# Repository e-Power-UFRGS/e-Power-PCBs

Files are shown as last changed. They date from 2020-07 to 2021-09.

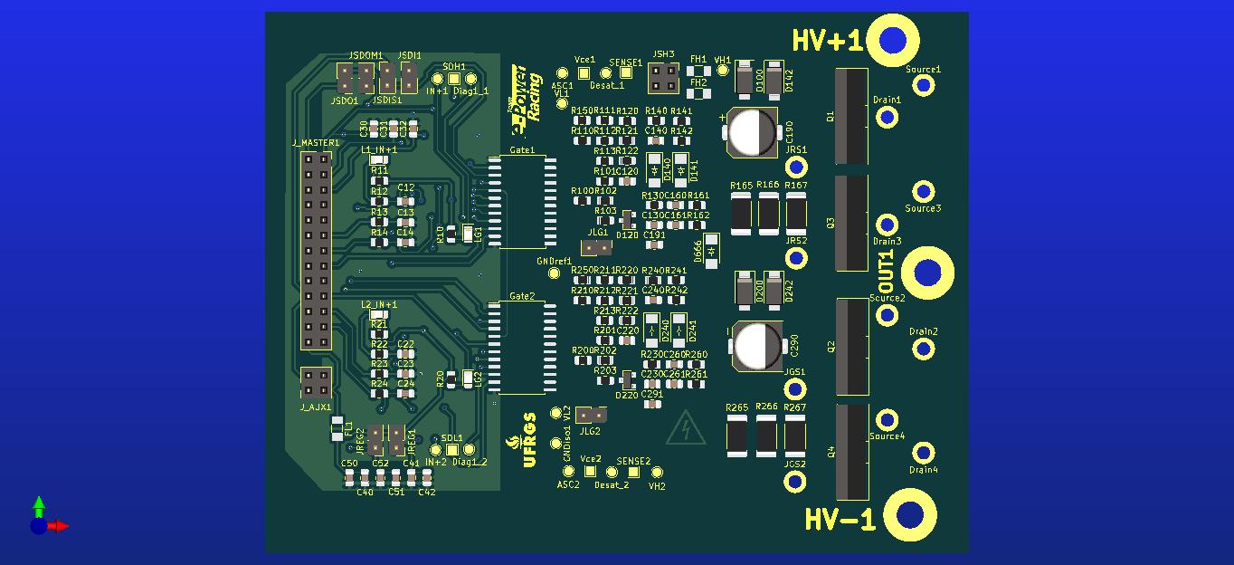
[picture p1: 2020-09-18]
Inversor/Gate_Driver_V2.jpg

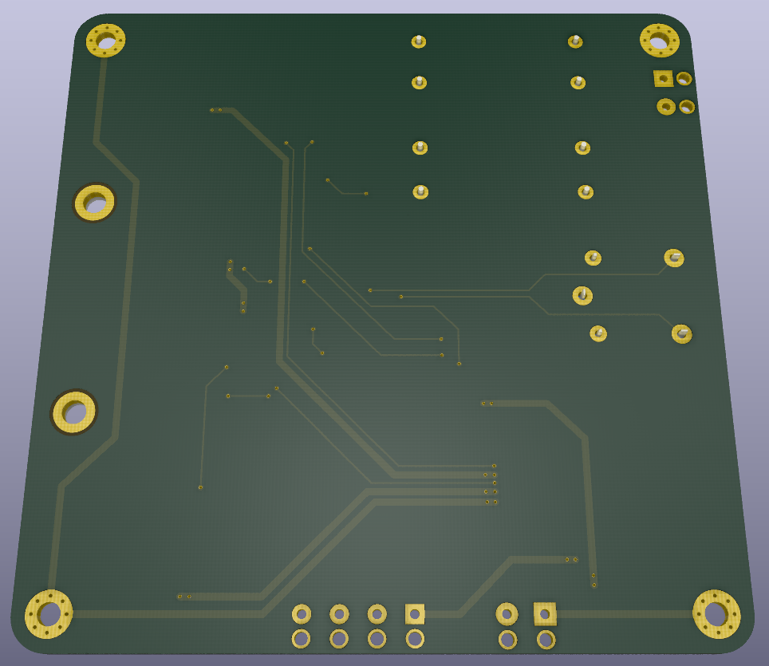
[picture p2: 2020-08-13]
TSAL/3d-renders/Screenshot_297.png

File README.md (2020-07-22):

# e-Power-PCBs

## Index

#### e-Power_conventions: Standard conventions for all PCBs
The image shows an example with conventions regarding the description data of the PCBs. One way to implemment this conventions is oppening 2 KiCad Pcbnew windows, one with the file you want to update and other with the e-Power_conventions.kicad_pcb and the copy the standard from one window to the other (yes, this is possible on the current versions of KiCad!).

descriptive_conventions

#### BMS_20S: Battery Management System with 20S measurement capability

#### TSAL: Tractive System Alternating Lights 

## License
[MIT](https://choosealicense.com/licenses/mit/)

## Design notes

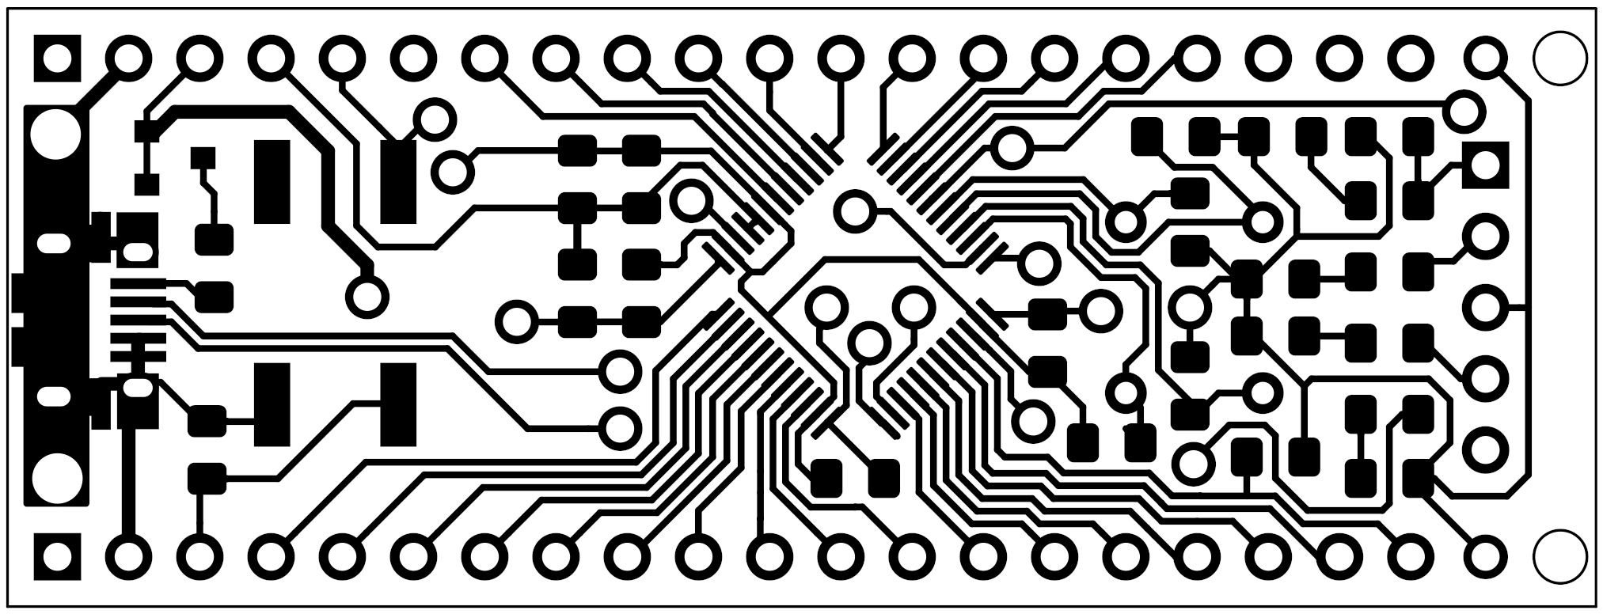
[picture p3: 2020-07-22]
UFRGS-PILL/front/UFRGS PILL-brd.jpg

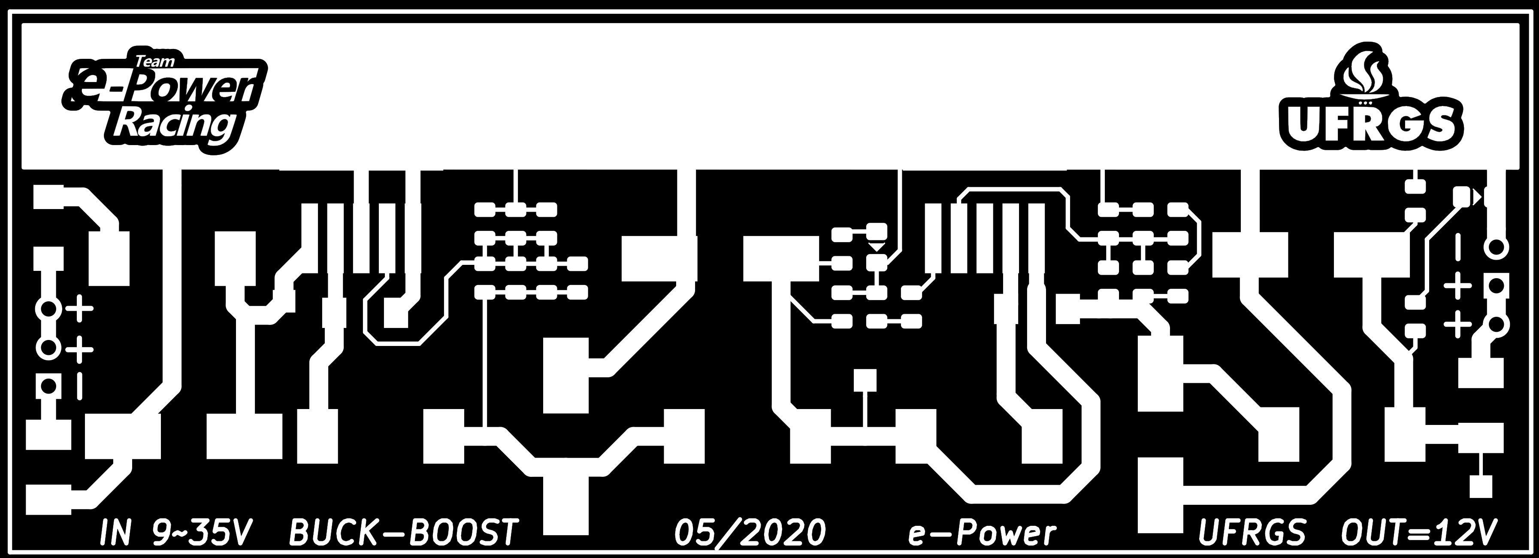
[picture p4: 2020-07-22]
BUCK-BOOST/BUCK-BOOST KiCad-brd_invert.jpg

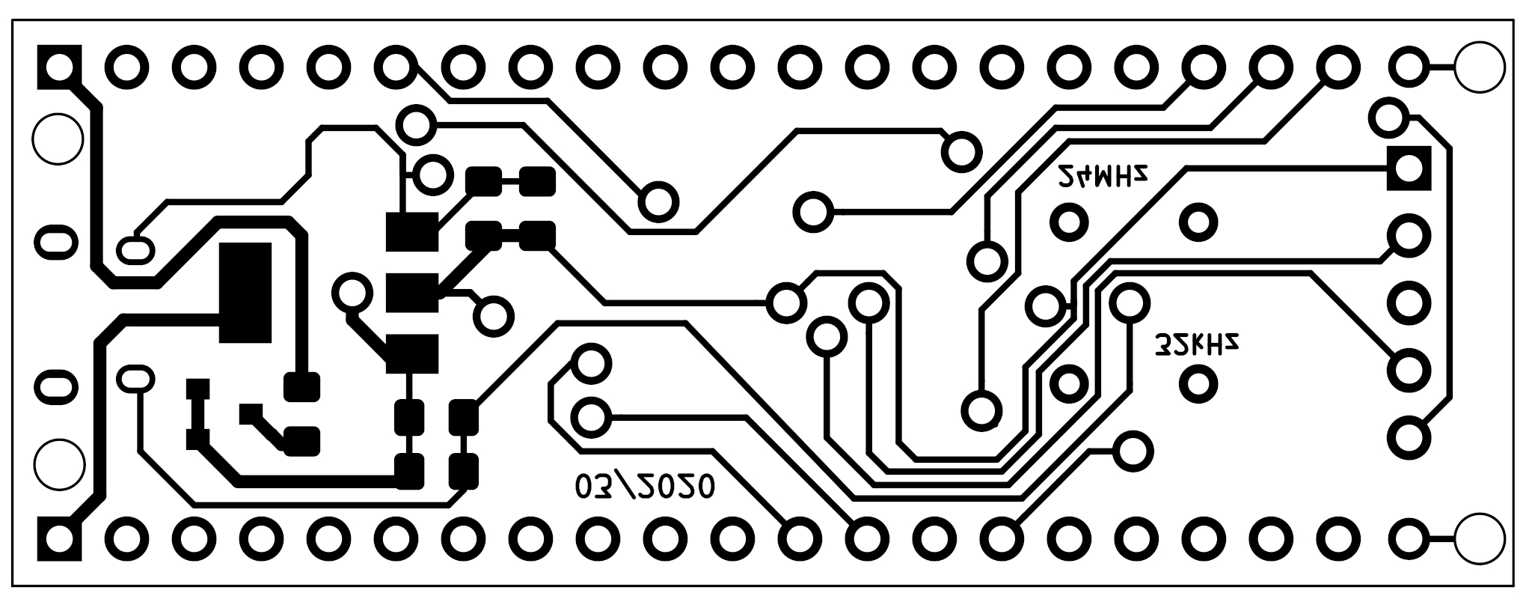
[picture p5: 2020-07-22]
UFRGS-PILL/back/UFRGS PILL-brd.jpg

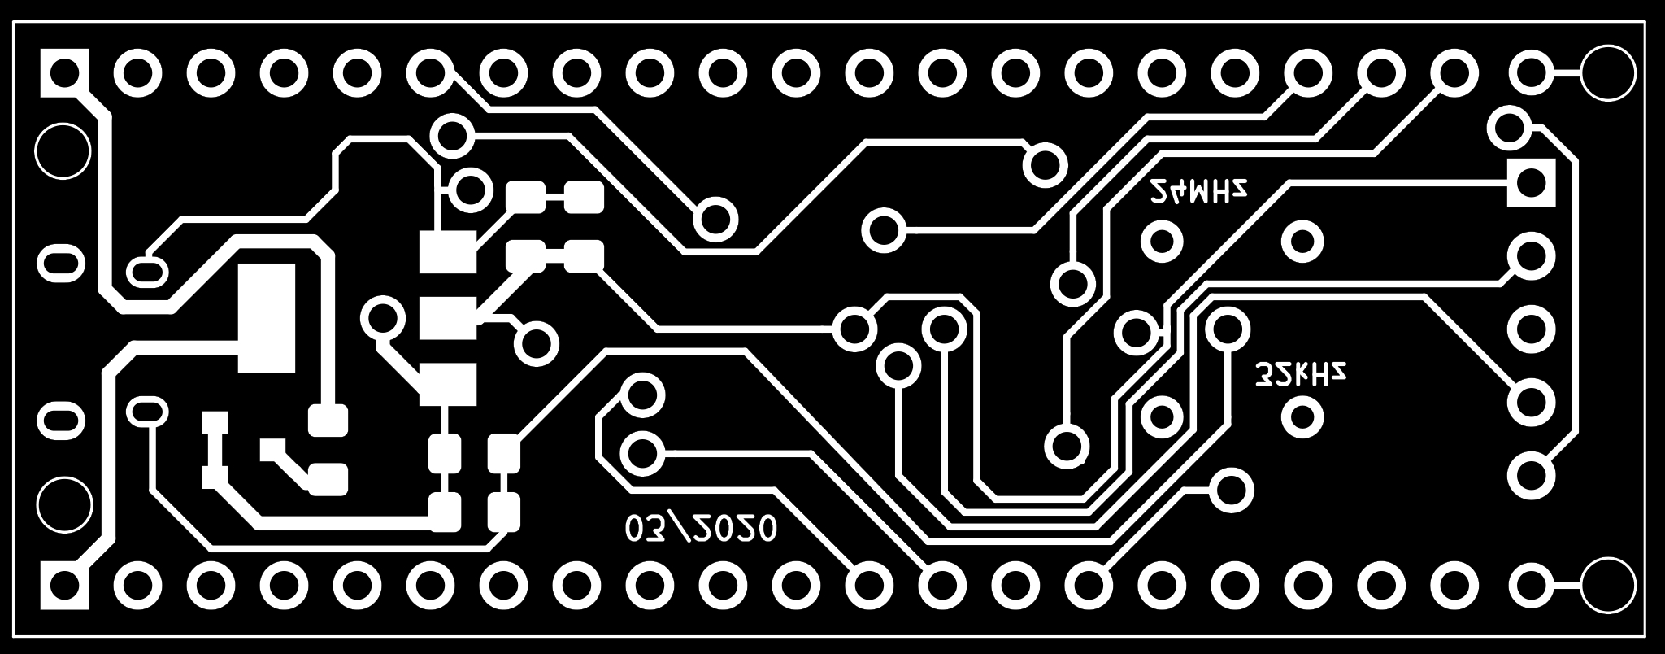
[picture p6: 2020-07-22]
UFRGS-PILL/back/UFRGS PILL-brd_invert.jpg

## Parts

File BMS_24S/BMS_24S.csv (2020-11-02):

Reference | Quantity | Value | Footprint | Datasheet | LCSC | Power | Precision | Voltage
C106 C103 C101 C107 C104 C102 C108 C113 C118 C126 C125 C115 C119 C120 C121 C122 C105 C116 C117 C206 C201 C207 C204 C209 C211 C301 C306 C309 C501 C502 C503 C601 C602 C603 C701 C702 C703 C801 C802 C803 C901 C902 C903 C1001 C1002 C1003 C1101 C1102 C1103 C1201 C1202 C1203 C1301 C1302 C1303 C1401 C1402 C1403 C1501 C1502 C1503 C1601 C1602 C1603 C1801 C1901 C2001 C2101 C2201 C2301 C3101 | 71 | 100nF | Capacitor_SMD:C_0805_2012Metric | https://datasheet.lcsc.com/szlcsc/YAGEO-CC0805KRX7R9BB104_C49678.pdf | C49678 |  | 10% | 50V
C109 C110 | 2 | 12pF | Capacitor_SMD:C_0805_2012Metric | Guangdong-Fenghua-Advanced-Tech-0805CG120J500NT_C1792.pdf | C1792 |  | 10% | 50V
C112 C111 | 2 | 100pF | Capacitor_SMD:C_0805_2012Metric | Samsung-Electro-Mechanics-CL21C101JBANNNC_C1790.pdf | C1790 |  | 10% | 50V
C114 C123 C124 C127 C205 C208 C202 C203 C210 C302 | 10 | 10uF | Capacitor_SMD:C_0805_2012Metric | ~ | C15850
C303 C307 C304 C305 C308 | 5 | 220uF | Capacitor_SMD:CP_Elec_10x10 | ~
D108 D107 D106 D105 D104 D103 D102 D101 D302 D2503 D2504 D2502 D2501 D2603 D2604 D2602 D2601 D2703 D2704 D2702 D2701 D2803 D2804 D2802 D2801 D2903 D2904 D2902 D2901 D3003 D3004 D3002 D3001 | 33 | LED | e-Power:LED_0805_1.15x1.40mm_HandSolder | ~
D301 | 1 | SS54HF | e-Power:DO-214AC | https://www.diodes.com/assets/Datasheets/ds23001.pdf
D501 D502 D503 D504 D505 D506 D601 D602 D603 D604 D605 D606 D701 D702 D703 D704 D705 D706 D801 D802 D803 D804 D805 D806 D901 D902 D903 D904 D905 D906 D1001 D1002 D1003 D1004 D1005 D1006 D1101 D1102 D1103 D1104 D1105 D1106 D1201 D1202 D1203 D1204 D1205 D1206 D1301 D1302 D1303 D1304 D1305 D1306 D1401 D1402 D1403 D1404 D1405 D1406 D1501 D1502 D1503 D1504 D1505 D1506 D1601 D1602 D1603 D1604 D1605 D1606 | 72 | LL4148 | e-Power:SOD-80 | http://www.vishay.com/docs/85557/ll4148.pdf | C9808
F301 | 1 | Fuse_1206 | e-Power:FUSE_1206_3216Metric | ~
F414 F416 F420 F422 F424 F426 F425 F423 F421 F419 F417 F415 F413 F411 F409 F407 F405 F403 F401 F402 F404 F406 F408 F410 F412 F418 | 26 | Fuse | e-Power:FUSE_1206_3216Metric | ~
FB101 FB301 FB302 FB303 FB304 FB305 FB306 FB307 FB308 FB309 FB310 | 11 | Ferrite_Bead | e-Power:FB_0805_2012Metric | ~ | C1017
G101 | 1 | Logo_UFRGS_Large | e-Power:Logo_UFRGS_22.0x12.0mm_Mask
G102 | 1 | Logo_e-Power_Large | e-Power:Logo_e-Power_22.8x12.0mm_SilkS
G103 | 1 | Logo_UFRGS_Large | e-Power:Logo_UFRGS_22.0x12.0mm_SilkS
G104 | 1 | SYM_LASER_Large | Symbol:WEEE-Logo_8.4x12mm_SilkScreen | ~
G105 | 1 | SYM_LASER_Large | Symbol:KiCad-Logo_12mm_SilkScreen | ~
G106 | 1 | SYM_ESD_Large | Symbol:ESD-Logo_13.2x12mm_SilkScreen | ~
H101 H102 H103 H104 | 4 | GND | e-Power:MountingHole_3.2mm_M3_Pad_Via | ~
J101 | 1 | Conn_01x08_Male | e-Power:Molex_Mini-Fit_Jr_2x04_P4.20mm_Horizontal | ~
J102 | 1 | ST-LINK | Connector_PinHeader_2.54mm:PinHeader_1x05_P2.54mm_Vertical | ~
J1701 | 1 | TEMP_IDC_26_CONN | Connector_IDC:IDC-Header_2x13_P2.54mm_Horizontal | ~
J3101 | 1 | Current_Conn | Connector_PinHeader_2.54mm:PinHeader_1x04_P2.54mm_Horizontal | ~
J3102 | 1 | BSPD_Conn | Connector_PinHeader_2.54mm:PinHeader_1x04_P2.54mm_Horizontal | ~
J401 | 1 | VOLT_IDC_26_CONN | Connector_IDC:IDC-Header_2x13_P2.54mm_Horizontal | ~
JP3101 | 1 | Jumper | Jumper:SolderJumper-2_P1.3mm_Open_TrianglePad1.0x1.5mm | ~
JP501 JP503 JP502 JP601 JP603 JP602 JP701 JP703 JP702 JP801 JP803 JP802 JP901 JP903 JP902 JP1001 JP1003 JP1002 JP1101 JP1103 JP1102 JP1201 JP1203 JP1202 JP1301 JP1303 JP1302 JP1401 JP1403 JP1402 JP1501 JP1503 JP1502 JP1601 JP1603 JP1602 | 36 | 0R | e-Power:zero_ohm_resistor_0805 | ~ |  | 1/8W | 1% | 150V
Q101 | 1 | MMBT3904 | Package_TO_SOT_SMD:SOT-23 | Changjiang-Electronics-Tech-CJ-MMBT5401_C8326.pdf | C20526
Q201 | 1 | MMBT5401 | Package_TO_SOT_SMD:SOT-23 | https://datasheet.lcsc.com/szlcsc/Changjiang-Electronics-Tech-CJ-MMBT5401_C8326.pdf | C8326
Q2501 Q2502 Q2503 Q2504 Q2601 Q2602 Q2603 Q2604 Q2701 Q2702 Q2703 Q2704 Q2801 Q2802 Q2803 Q2804 Q2901 Q2902 Q2903 Q2904 Q3001 Q3002 Q3003 Q3004 | 24 | Si2302DS | Package_TO_SOT_SMD:SOT-23 | https://www.vishay.com/docs/70628/70628.pdf
R107 R105 R101 R108 R106 R102 R149 R147 R139 R137 R121 R119 R133 R132 R131 R130 R103 R129 R128 R127 R126 R216 R217 R218 R229 R212 R219 R204 R214 R221 R206 R226 R228 R225 R208 R202 R215 R313 R301 R302 R303 R305 R306 R506 R504 R503 R502 R501 R508 R507 R514 R512 R511 R510 R509 R513 R516 R515 R505 R606 R604 R603 R602 R601 R608 R607 R614 R612 R611 R610 R609 R613 R616 R615 R605 R706 R704 R703 R702 R701 R708 R707 R714 R712 R711 R710 R709 R713 R716 R715 R705 R806 R804 R803 R802 R801 R808 R807 R814 R812 R811 R810 R809 R813 R816 R815 R805 R906 R904 R903 R902 R901 R908 R907 R914 R912 R911 R910 R909 R913 R916 R915 R905 R1006 R1004 R1003 R1002 R1001 R1008 R1007 R1014 R1012 R1011 R1010 R1009 R1013 R1016 R1015 R1005 R1106 R1104 R1103 R1102 R1101 R1108 R1107 R1114 R1112 R1111 R1110 R1109 R1113 R1116 R1115 R1105 R1206 R1204 R1203 R1202 R1201 R1208 R1207 R1214 R1212 R1211 R1210 R1209 R1213 R1216 R1215 R1205 R1306 R1304 R1303 R1302 R1301 R1308 R1307 R1314 R1312 R1311 R1310 R1309 R1313 R1316 R1315 R1305 R1406 R1404 R1403 R1402 R1401 R1408 R1407 R1414 R1412 R1411 R1410 R1409 R1413 R1416 R1415 R1405 R1506 R1504 R1503 R1502 R1501 R1508 R1507 R1514 R1512 R1511 R1510 R1509 R1513 R1516 R1515 R1505 R1606 R1604 R1603 R1602 R1601 R1608 R1607 R1614 R1612 R1611 R1610 R1609 R1613 R1616 R1615 R1605 R1803 R1801 R1804 R1802 R1903 R1901 R1904 R1902 R2003 R2001 R2004 R2002 R2103 R2101 R2104 R2102 R2203 R2201 R2204 R2202 R2303 R2301 R2304 R2302 R2543 R2529 R2515 R2501 R2643 R2629 R2615 R2601 R2743 R2729 R2715 R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 | 283 | 1K | Resistor_SMD:R_0805_2012Metric | https://datasheet.lcsc.com/szlcsc/Uniroyal-Elec-0805W8F1001T5E_C17513.pdf | C17513 | 1/8W | 1% | 150V
R110 R201 R210 | 3 | 100R | Resistor_SMD:R_0805_2012Metric | Uniroyal-Elec-0805W8F1000T5E_C17408.pdf | C17408 | 1/8W | 1% | 150V
R112 R111 | 2 | 10R | Resistor_SMD:R_0805_2012Metric | 1812121441_Uniroyal-Elec-0805W8F100JT5E_C17415.pdf | C17415 | 1/8W | 1% | 150V
R114 R115 R116 R117 R113 R118 R124 R125 R134 R135 R123 R136 R142 R143 R144 R145 R141 R146 R150 R148 R140 R138 R122 R120 R109 R104 R230 R224 R2556 R2542 R2528 R2514 R2656 R2642 R2628 R2614 R2756 R2742 R2728 R2714 R2856 R2842 R2828 R2814 R2956 R2942 R2928 R2914 R3056 R3042 R3028 R3014 R3103 R3104 R3105 R3102 | 56 | 10K | Resistor_SMD:R_0805_2012Metric | https://datasheet.lcsc.com/szlcsc/Uniroyal-Elec-0805W8F1001T5E_C17513.pdf | C17414 | 1/8W | 1% | 150V
R209 R220 R203 R222 R223 R227 R213 R1702 R1703 R1704 R1705 R1706 R1707 R1708 R1709 R1710 R1711 R1712 R1715 R1713 R1714 R1716 R1717 R1718 R1719 R1720 R1721 R1722 R1723 R1724 R1725 R1726 R1701 R3101 | 34 | 0R | Resistor_SMD:R_0805_2012Metric | ~ | C17477
R211 R205 R207 | 3 | 100K | Resistor_SMD:R_0805_2012Metric | ~ | C17407
R2549 R2550 R2551 R2552 R2553 R2548 R2547 R2535 R2536 R2537 R2538 R2539 R2534 R2533 R2521 R2522 R2523 R2524 R2525 R2520 R2519 R2507 R2508 R2509 R2506 R2505 R2510 R2511 R2504 R2503 R2502 R2518 R2517 R2516 R2532 R2531 R2530 R2546 R2545 R2544 R2649 R2650 R2651 R2652 R2653 R2648 R2647 R2635 R2636 R2637 R2638 R2639 R2634 R2633 R2621 R2622 R2623 R2624 R2625 R2620 R2619 R2607 R2608 R2609 R2606 R2605 R2610 R2611 R2604 R2603 R2602 R2618 R2617 R2616 R2632 R2631 R2630 R2646 R2645 R2644 R2749 R2750 R2751 R2752 R2753 R2748 R2747 R2735 R2736 R2737 R2738 R2739 R2734 R2733 R2721 R2722 R2723 R2724 R2725 R2720 R2719 R2707 R2708 R2709 R2706 R2705 R2710 R2711 R2704 R2703 R2702 R2718 R2717 R2716 R2732 R2731 R2730 R2746 R2745 R2744 R2849 R2850 R2851 R2852 R2853 R2848 R2847 R2835 R2836 R2837 R2838 R2839 R2834 R2833 R2821 R2822 R2823 R2824 R2825 R2820 R2819 R2807 R2808 R2809 R2806 R2805 R2810 R2811 R2804 R2803 R2802 R2818 R2817 R2816 R2832 R2831 R2830 R2846 R2845 R2844 R2949 R2950 R2951 R2952 R2953 R2948 R2947 R2935 R2936 R2937 R2938 R2939 R2934 R2933 R2921 R2922 R2923 R2924 R2925 R2920 R2919 R2907 R2908 R2909 R2906 R2905 R2910 R2911 R2904 R2903 R2902 R2918 R2917 R2916 R2932 R2931 R2930 R2946 R2945 R2944 R3049 R3050 R3051 R3052 R3053 R3048 R3047 R3035 R3036 R3037 R3038 R3039 R3034 R3033 R3021 R3022 R3023 R3024 R3025 R3020 R3019 R3007 R3008 R3009 R3006 R3005 R3010 R3011 R3004 R3003 R3002 R3018 R3017 R3016 R3032 R3031 R3030 R3046 R3045 R3044 | 240 | 100R | Resistor_SMD:R_2512_6332Metric | ~
R2555 R2541 R2527 R2513 R2540 R2554 R2526 R2512 R2655 R2641 R2627 R2613 R2640 R2654 R2626 R2612 R2755 R2741 R2727 R2713 R2740 R2754 R2726 R2712 R2855 R2841 R2827 R2813 R2840 R2854 R2826 R2812 R2955 R2941 R2927 R2913 R2940 R2954 R2926 R2912 R3055 R3041 R3027 R3013 R3040 R3054 R3026 R3012 | 48 | 330R | Resistor_SMD:R_0805_2012Metric | ~
R307 R308 R309 R310 R311 R312 R315 R316 R317 | 9 | 1R | Resistor_SMD:R_0805_2012Metric | https://datasheet.lcsc.com/szlcsc/Uniroyal-Elec-0805W8F1001T5E_C17513.pdf | C25271 | 1/8W | 1% | 150V
R314 R304 | 2 | ADJ | Resistor_SMD:R_0805_2012Metric | ~
SW101 | 1 | SW_Push | Button_Switch_SMD:SW_Push_1P1T_NO_6x6mm_H9.5mm | ~
TP101 | 1 | B1 | e-Power:TestPoint_Pad_D1.0mm | ~
TP102 | 1 | B2 | e-Power:TestPoint_Pad_D1.0mm | ~
TP103 | 1 | B3 | e-Power:TestPoint_Pad_D1.0mm | ~
TP104 | 1 | B4 | e-Power:TestPoint_Pad_D1.0mm | ~
TP105 | 1 | B5 | e-Power:TestPoint_Pad_D1.0mm | ~
TP106 | 1 | B6 | e-Power:TestPoint_Pad_D1.0mm | ~
TP107 | 1 | B7 | e-Power:TestPoint_Pad_D1.0mm | ~
TP108 | 1 | B8 | e-Power:TestPoint_Pad_D1.0mm | ~
TP109 | 1 | B9 | e-Power:TestPoint_Pad_D1.0mm | ~
TP110 | 1 | B10 | e-Power:TestPoint_Pad_D1.0mm | ~
TP111 | 1 | B11 | e-Power:TestPoint_Pad_D1.0mm | ~
TP112 | 1 | B12 | e-Power:TestPoint_Pad_D1.0mm | ~
TP113 | 1 | B13 | e-Power:TestPoint_Pad_D1.0mm | ~
TP114 | 1 | B14 | e-Power:TestPoint_Pad_D1.0mm | ~
TP115 | 1 | B15 | e-Power:TestPoint_Pad_D1.0mm | ~
TP116 | 1 | B16 | e-Power:TestPoint_Pad_D1.0mm | ~
TP117 | 1 | B17 | e-Power:TestPoint_Pad_D1.0mm | ~
TP118 | 1 | B18 | e-Power:TestPoint_Pad_D1.0mm | ~
TP119 | 1 | B19 | e-Power:TestPoint_Pad_D1.0mm | ~
TP120 | 1 | B20 | e-Power:TestPoint_Pad_D1.0mm | ~
TP121 | 1 | B21 | e-Power:TestPoint_Pad_D1.0mm | ~
TP122 | 1 | B22 | e-Power:TestPoint_Pad_D1.0mm | ~
TP123 | 1 | B23 | e-Power:TestPoint_Pad_D1.0mm | ~
TP124 | 1 | B24 | e-Power:TestPoint_Pad_D1.0mm | ~
TP125 TP127 TP133 TP138 TP203 TP309 TP310 | 7 | GND | e-Power:TestPoint_Pad_D1.0mm | ~
TP126 TP132 | 2 | VCC | e-Power:TestPoint_Pad_D1.0mm | ~
TP128 | 1 | CAN_L | e-Power:TestPoint_Pad_D1.0mm | ~
TP129 | 1 | CAN_H | e-Power:TestPoint_Pad_D1.0mm | ~
TP130 | 1 | CAN_GND | e-Power:TestPoint_Pad_D1.0mm | ~
TP131 | 1 | ~ERROR | e-Power:TestPoint_Pad_D1.0mm | ~
TP134 TP161 | 2 | T_SWCLK | e-Power:TestPoint_Pad_D1.0mm | ~
TP135 TP163 | 2 | 3.3V | e-Power:TestPoint_Pad_D1.0mm | ~
TP136 | 1 | NRST | e-Power:TestPoint_Pad_D1.0mm | ~
TP137 TP160 | 2 | T_SWDIO | e-Power:TestPoint_Pad_D1.0mm | ~
TP139 | 1 | VOUT_1P | e-Power:TestPoint_Pad_D1.0mm | ~
TP140 | 1 | VOUT_2P | e-Power:TestPoint_Pad_D1.0mm | ~
TP141 | 1 | VOUT_3P | e-Power:TestPoint_Pad_D1.0mm | ~
TP142 | 1 | TOUT_1P | e-Power:TestPoint_Pad_D1.0mm | ~
TP143 TP159 | 2 | ERROR_TRIG | e-Power:TestPoint_Pad_D1.0mm | ~
TP144 TP158 | 2 | V_ERROR | e-Power:TestPoint_Pad_D1.0mm | ~
TP145 TP157 | 2 | T_ERROR | e-Power:TestPoint_Pad_D1.0mm | ~
TP146 TP156 | 2 | C_ERROR | e-Power:TestPoint_Pad_D1.0mm | ~
TP147 | 1 | C1 | e-Power:TestPoint_Pad_D1.0mm | ~
TP148 | 1 | S | e-Power:TestPoint_Pad_D1.0mm | ~
TP149 | 1 | S0 | e-Power:TestPoint_Pad_D1.0mm | ~
TP150 | 1 | S1 | e-Power:TestPoint_Pad_D1.0mm | ~
TP151 | 1 | S2 | e-Power:TestPoint_Pad_D1.0mm | ~
TP152 | 1 | TX | e-Power:TestPoint_Pad_D1.0mm | ~
TP153 | 1 | TOUT_3P | e-Power:TestPoint_Pad_D1.0mm | ~
TP154 | 1 | RX | e-Power:TestPoint_Pad_D1.0mm | ~
TP155 | 1 | TOUT_2P | e-Power:TestPoint_Pad_D1.0mm | ~
TP162 | 1 | PB3 | e-Power:TestPoint_Pad_D1.0mm | ~
TP201 | 1 | 1.8V | e-Power:TestPoint_Pad_D1.0mm | ~
TP202 | 1 | 5.000V | e-Power:TestPoint_Pad_D1.0mm | ~
TP204 | 1 | 0.850V | e-Power:TestPoint_Pad_D1.0mm | ~
TP205 | 1 | 2.2727V | e-Power:TestPoint_Pad_D1.0mm | ~
TP301 | 1 | +VIN | e-Power:TestPoint_Pad_D1.0mm | ~
TP302 | 1 | +12V | e-Power:TestPoint_Pad_D1.0mm | ~
TP303 TP304 | 2 | +5V | e-Power:TestPoint_Pad_D1.0mm | ~
TP306 TP305 | 2 | +3.3V | e-Power:TestPoint_Pad_D1.0mm | ~
TP307 | 1 | +C | e-Power:TestPoint_Pad_D1.0mm | ~
TP308 | 1 | -C | e-Power:TestPoint_Pad_D1.0mm | ~
U105 U103 U101 U106 U104 U102 | 6 | 74HC4051 | Package_SO:SOP-16_4.4x10.4mm_P1.27mm | http://www.ti.com/lit/ds/symlink/cd74hc4051.pdf | C9386
U107 U109 U111 | 3 | 74HC595 | Package_SO:SOP-16_4.4x10.4mm_P1.27mm | http://www.ti.com/lit/ds/symlink/sn74hc595.pdf | C5947
U108 | 1 | STM32G431CBTx | Package_QFP:LQFP-48_7x7mm_P0.5mm
U110 | 1 | MCP2558 | Package_SO:SOIC-8_3.9x4.9mm_P1.27mm | https://ww1.microchip.com/downloads/en/DeviceDoc/20005533A.pdf
U112 U113 U201 U1801 U1901 U2001 U2101 U2201 U2301 U3101 | 10 | LM324 | Package_SO:SOIC-14_3.9x8.7mm_P1.27mm | http://www.ti.com/lit/ds/symlink/lm2902-n.pdf | C71035
U203 U202 U204 | 3 | TL431 | Package_TO_SOT_SMD:SOT-23 | http://www.ti.com/lit/ds/symlink/tl431.pdf | C3113
U301 | 1 | LM317 | e-Power:TO-220-3_Horizontal_TabDown | http://www.ti.com/lit/ds/symlink/lm317.pdf
U302 | 1 | AP1117-33 | Package_TO_SOT_SMD:SOT-223-3_TabPin2 | http://www.diodes.com/datasheets/AP1117.pdf | C6186
U501 U503 U601 U603 U701 U703 U801 U803 U901 U903 U1001 U1003 U1101 U1103 U1201 U1203 U1301 U1303 U1401 U1403 U1501 U1503 U1601 U1603 | 24 | TS1851ILT | Package_TO_SOT_SMD:SOT-23-5_HandSoldering | https://www.st.com/resource/en/datasheet/ts1851.pdf
U502 U602 U702 U802 U902 U1002 U1102 U1202 U1302 U1402 U1502 U1602 U2501 U2601 U2701 U2801 U2901 U3001 | 18 | TLP290-4 | e-Power:SOIC-16_4.55x10.3mm_P1.27mm(TLP290-4) | https://toshiba.semicon-storage.com/info/docget.jsp?did=12855&prodName=TLP290-4 | C39031
Y101 | 1 | 24MHz | Crystal:Crystal_HC52-6mm_Vertical | ~
Y102 | 1 | 32.768KHz | Crystal:Crystal_HC52-6mm_Vertical | ~

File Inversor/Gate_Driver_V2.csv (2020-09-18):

Id | Nome | Pacote | Quantidade | Valor | Colunas1
1 | C10,C3,C4,C8,C22,C23 | CP_Radial_D4.0mm_P1.50mm | 6 | D.N.M.
5 | C1,C6 | CP_Radial_D4.0mm_P1.50mm | 2 | 1n/25v
6 | C2,C7 | CP_Radial_D4.0mm_P1.50mm | 2 | 150pF/50v
8 | C9,C13,C15,C40,C41,C42 | CP_Radial_D4.0mm_P1.50mm | 6 | 100pF
9 | C19,C31 | CP_Radial_D4.0mm_P1.50mm | 2 | 4.7u/6.3v
10 | C21 | CP_Radial_D4.0mm_P1.50mm | 1 | 47pF
11 | C29,C39 | CP_Radial_D4.0mm_P1.50mm | 2 | 100n/50v
12 | C32 | CP_Radial_D4.0mm_P1.50mm | 1 | C
13 | C36,C38 | CP_Radial_D4.0mm_P1.50mm | 2 | 100n/6.3v
14 | C37 | CP_Radial_D4.0mm_P1.50mm | 1 | 100n/4v
47 | D1,D6 | D_A-405_P7.62mm_Horizontal | 2 | STTH112A | 1200v/1A
48 | D2,D7 | D_A-405_P7.62mm_Horizontal | 2 | BAT20JFILM | 23V/1A
49 | D3,D8 | D_A-405_P7.62mm_Horizontal | 2 | STPS2H100A | 100v/2A
50 | D5,D10 | D_A-405_P7.62mm_Horizontal | 2 | D.N.M.
51 | D11 | D_A-405_P7.62mm_Horizontal | 1 | D
16 | DL1,DL2,DL3,DL4 | LED_D3.0mm_Clear | 4 | RED
18 | J6 | PhoenixContact_MCV_1,5_2-G-5.08_1x02_P5.08mm_Vertical | 1 | Screw_Terminal_01x02
19 | J7,J2 | PhoenixContact_MCV_1,5_3-G-5.08_1x03_P5.08mm_Vertical | 2 | Screw_Terminal_01x03
20 | JP1,JP2,JP5,JP6,JP7,JP11,JP12 | PinHeader_1x02_P1.00mm_Vertical | 7 | OPEN
21 | JP3 | PinHeader_1x02_P1.00mm_Vertical | 1 | CLOSED
22 | JP4 | PinHeader_1x02_P1.00mm_Vertical | 1 | 3.3v-VDD
17 | J3 | PinSocket_1x09_P1.27mm_Vertical | 1 | Conn_01x09_Male
26 | R3,R5,R24,R26 | Potentiometer_Bourns_3266Y_Vertical | 4 | 20R
24 | R1,R7,R9,R22,R28,R30 | R_Axial_DIN0204_L3.6mm_D1.6mm_P5.08mm_Horizontal | 6 | 1K
25 | R2,R15,R23,R32 | R_Axial_DIN0204_L3.6mm_D1.6mm_P5.08mm_Horizontal | 4 | 0R
27 | R8,R17,R19,R20,R21,R29,R33,R35,R36,R37 | R_Axial_DIN0204_L3.6mm_D1.6mm_P5.08mm_Horizontal | 10 | 0.2R/2W/1%
28 | R10,R31 | R_Axial_DIN0204_L3.6mm_D1.6mm_P5.08mm_Horizontal | 2 | D.N.M.
29 | R11,R40 | R_Axial_DIN0204_L3.6mm_D1.6mm_P5.08mm_Horizontal | 2 | 750R
30 | R12,R13,R16,R38,R39,R41 | R_Axial_DIN0204_L3.6mm_D1.6mm_P5.08mm_Horizontal | 6 | 100R
31 | R14,R42 | R_Axial_DIN0204_L3.6mm_D1.6mm_P5.08mm_Horizontal | 2 | 750R
32 | R18,R34 | R_Axial_DIN0204_L3.6mm_D1.6mm_P5.08mm_Horizontal | 2 | 50K
45 | U1,U2 | SOIC127P1032X265-24N | 2 | STGAP1AS
15 | D4,D9 | SOT-23 | 2 | BAT54S | 40v/300mA
3 | J4 | TE_MATE-N-LOK_1-794067-x_2x07_P4.14mm_Vertical | 1 | Conn_01x14_Male
4 | J5 | TE_MATE-N-LOK_1-794067-x_2x07_P4.14mm_Vertical | 1 | MASTER
46 | J1 | TE_MATE-N-LOK_1-794067-x_2x07_P4.14mm_Vertical | 1 | SLAVE
2 | TP7 | TestPoint_Keystone_5010-5014_Multipurpose | 1 | CLAMP_2
33 | TP1 | TestPoint_Keystone_5010-5014_Multipurpose | 1 | GND
34 | TP2 | TestPoint_Keystone_5010-5014_Multipurpose | 1 | ASC_1
35 | TP3 | TestPoint_Keystone_5010-5014_Multipurpose | 1 | CLAMP_1
36 | TP4 | TestPoint_Keystone_5010-5014_Multipurpose | 1 | SNS_1
37 | TP5 | TestPoint_Keystone_5010-5014_Multipurpose | 1 | DESAT_1
38 | TP6 | TestPoint_Keystone_5010-5014_Multipurpose | 1 | ASC_2
39 | TP8 | TestPoint_Keystone_5010-5014_Multipurpose | 1 | SNS_2
40 | TP9 | TestPoint_Keystone_5010-5014_Multipurpose | 1 | DESAT_2
41 | TP10 | TestPoint_Keystone_5010-5014_Multipurpose | 1 | GNDi_1
42 | TP11 | TestPoint_Keystone_5010-5014_Multipurpose | 1 | GNDi_2
43 | TP13,TP17 | TestPoint_Keystone_5010-5014_Multipurpose | 2 | VH
44 | TP19 | TestPoint_Keystone_5010-5014_Multipurpose | 1 | VDD
23 | Q1,Q2,Q3,Q4 | TO-247-3_Vertical | 4 | STGW40H120DF2

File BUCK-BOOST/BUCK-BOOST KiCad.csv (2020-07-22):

Source: | C:\Users\gabri\GoogleDrive\E-POWER\Eletronica\BUCK-BOOST\BUCK-BOOST KiCad\BUCK-BOOST KiCad.sch
Date: | 7/4/2020 12:26:07 AM
Tool: | Eeschema (5.1.5)-3
Generator: | C:\Program Files\KiCad\bin\scripting\plugins/bom_csv_grouped_by_value.py
Component Count: | 40
Individual Components:
Item | Qty | Reference(s) | Value | LibPart | Footprint | Datasheet | LCSC
 |  | C101 | 100nF | Device:C | Capacitor_SMD:C_0805_2012Metric | ~
 |  | C102 | 100nF | Device:C | Capacitor_SMD:C_0805_2012Metric | ~
 |  | C103 | 470uF | Device:CP | e-Power:CP_Elec_10x10 | ~
 |  | C104 | 100nF | Device:C | Capacitor_SMD:C_0805_2012Metric | ~
 |  | C105 | 220uF | Device:CP | e-Power:CP_Elec_10x10 | ~
 |  | C106 | 470uF | Device:CP | e-Power:CP_Elec_10x10 | ~
 |  | C107 | 100nF | Device:C | Capacitor_SMD:C_0805_2012Metric | ~
 |  | C108 | 220uF | Device:CP | e-Power:CP_Elec_10x10 | ~
 |  | C109 | 470uF | Device:CP | e-Power:CP_Elec_10x10 | ~
 |  | C110 | 100nF | Device:C | Capacitor_SMD:C_0805_2012Metric | ~
 |  | C111 | 100nF | Device:C | Capacitor_SMD:C_0805_2012Metric | ~
 |  | D101 | SS54HF | e-Power:D_SCH_SS54HF | e-Power:DO-214AC | https://br.mouser.com/datasheet/2/80/20190806165140-1729178.pdf | C22452
 |  | D102 | SS54HF | e-Power:D_SCH_SS54HF | e-Power:DO-214AC | https://br.mouser.com/datasheet/2/80/20190806165140-1729178.pdf | C22452
 |  | D103 | SS54HF | e-Power:D_SCH_SS54HF | e-Power:DO-214AC | https://br.mouser.com/datasheet/2/80/20190806165140-1729178.pdf | C22452
 |  | D104 | RED GRN | e-Power:LED | e-Power:LED_0805_1.15x1.40mm_HandSolder
 |  | D105 | RED LED | e-Power:LED | e-Power:LED_0805_1.15x1.40mm_HandSolder
 |  | F101 | Fuse | Device:Fuse | e-Power:Fuse_SMD | ~
 |  | F102 | Fuse | Device:Fuse | e-Power:Fuse_SMD | ~
 |  | J101 | BATTERY | Connector:Screw_Terminal_01x02 | Connector_PinHeader_2.54mm:PinHeader_1x02_P2.54mm_Vertical | ~
 |  | J102 | 12V | Connector:Screw_Terminal_01x02 | Connector_PinHeader_2.54mm:PinHeader_1x02_P2.54mm_Vertical | ~
 |  | L101 | 10uH | e-Power:INDUCTOR_PWR | e-Power:L_10.4x10.4_H4.8 | ~
 |  | L102 | 3uH | e-Power:INDUCTOR_PWR | e-Power:L_10.4x10.4_H4.8 | ~
 |  | L103 | 3uH | e-Power:INDUCTOR_PWR | e-Power:L_10.4x10.4_H4.8 | ~
 |  | L104 | 10uH | e-Power:INDUCTOR_PWR | e-Power:L_10.4x10.4_H4.8 | ~
 |  | L105 | 3uH | e-Power:INDUCTOR_PWR | e-Power:L_10.4x10.4_H4.8 | ~
 |  | R101 | 2K2 | Device:R | Resistor_SMD:R_0805_2012Metric | ~
 |  | R102 | 12K | Device:R | Resistor_SMD:R_0805_2012Metric | ~
 |  | R103 | 1K | Device:R | Resistor_SMD:R_0805_2012Metric | ~
 |  | R104 | 1K5 | Device:R | Resistor_SMD:R_0805_2012Metric | ~
 |  | R105 | ADJ | Device:R | Resistor_SMD:R_0805_2012Metric | ~
 |  | R106 | ADJ | Device:R | Resistor_SMD:R_0805_2012Metric | ~
 |  | R107 | ADJ | Device:R | Resistor_SMD:R_0805_2012Metric | ~
 |  | R108 | 1K5 | Device:R | Resistor_SMD:R_0805_2012Metric | ~
 |  | R109 | ADJ | Device:R | Resistor_SMD:R_0805_2012Metric | ~
 |  | R110 | 180K | Device:R | Resistor_SMD:R_0805_2012Metric | ~
 |  | R111 | 10K | Device:R | Resistor_SMD:R_0805_2012Metric | ~
 |  | R112 | 10K | Device:R | Resistor_SMD:R_0805_2012Metric | ~
 |  | R113 | 10K | Device:R | Resistor_SMD:R_0805_2012Metric | ~
 |  | U101 | LM2577S-ADJ | e-Power:LM2577S-ADJ | Package_TO_SOT_SMD:TO-263-5_TabPin3 | https://www.ti.com/lit/ds/symlink/lm2577.pdf?&ts=1589076847876
 |  | U102 | LM2596S-ADJ | Regulator_Switching:LM2596S-ADJ | Package_TO_SOT_SMD:TO-263-5_TabPin3 | http://www.ti.com/lit/ds/symlink/lm2596.pdf
Collated Components:
Item | Qty | Reference(s) | Value | LibPart | Footprint | Datasheet | LCSC
1 | 6 | C101, C102, C104, C107, C110, C111 | 100nF | Device:C | Capacitor_SMD:C_0805_2012Metric | ~
2 | 3 | C103, C106, C109 | 470uF | Device:CP | e-Power:CP_Elec_10x10 | ~
3 | 2 | C105, C108 | 220uF | Device:CP | e-Power:CP_Elec_10x10 | ~
4 | 3 | D101, D102, D103 | SS54HF | e-Power:D_SCH_SS54HF | e-Power:DO-214AC | https://br.mouser.com/datasheet/2/80/20190806165140-1729178.pdf | C22452
5 | 1 | D104 | RED GRN | e-Power:LED | e-Power:LED_0805_1.15x1.40mm_HandSolder
6 | 1 | D105 | RED LED | e-Power:LED | e-Power:LED_0805_1.15x1.40mm_HandSolder
7 | 2 | F101, F102 | Fuse | Device:Fuse | e-Power:Fuse_SMD | ~
8 | 1 | J101 | BATTERY | Connector:Screw_Terminal_01x02 | Connector_PinHeader_2.54mm:PinHeader_1x02_P2.54mm_Vertical | ~
9 | 1 | J102 | 12V | Connector:Screw_Terminal_01x02 | Connector_PinHeader_2.54mm:PinHeader_1x02_P2.54mm_Vertical | ~
10 | 2 | L101, L104 | 10uH | e-Power:INDUCTOR_PWR | e-Power:L_10.4x10.4_H4.8 | ~
11 | 3 | L102, L103, L105 | 3uH | e-Power:INDUCTOR_PWR | e-Power:L_10.4x10.4_H4.8 | ~
12 | 1 | R101 | 2K2 | Device:R | Resistor_SMD:R_0805_2012Metric | ~
13 | 1 | R102 | 12K | Device:R | Resistor_SMD:R_0805_2012Metric | ~
14 | 1 | R103 | 1K | Device:R | Resistor_SMD:R_0805_2012Metric | ~
15 | 2 | R104, R108 | 1K5 | Device:R | Resistor_SMD:R_0805_2012Metric | ~
16 | 4 | R105, R106, R107, R109 | ADJ | Device:R | Resistor_SMD:R_0805_2012Metric | ~
17 | 1 | R110 | 180K | Device:R | Resistor_SMD:R_0805_2012Metric | ~
18 | 3 | R111, R112, R113 | 10K | Device:R | Resistor_SMD:R_0805_2012Metric | ~
19 | 1 | U101 | LM2577S-ADJ | e-Power:LM2577S-ADJ | Package_TO_SOT_SMD:TO-263-5_TabPin3 | https://www.ti.com/lit/ds/symlink/lm2577.pdf?&ts=1589076847876
20 | 1 | U102 | LM2596S-ADJ | Regulator_Switching:LM2596S-ADJ | Package_TO_SOT_SMD:TO-263-5_TabPin3 | http://www.ti.com/lit/ds/symlink/lm2596.pdf

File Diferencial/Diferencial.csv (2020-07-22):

Source: | C:\Users\gabri\GoogleDrive\E-POWER\Eletronica\KiCad\Diferencial\Diferencial.sch
Date: | 7/4/2020 1:17:21 AM
Tool: | Eeschema (5.1.5)-3
Generator: | C:\Program Files\KiCad\bin\scripting\plugins/bom_csv_grouped_by_value.py
Component Count: | 64
Individual Components:
Item | Qty | Reference(s) | Value | LibPart | Footprint | Datasheet
 |  | C1 | 100n | Device:C | Capacitor_SMD:C_0805_2012Metric_Pad1.15x1.40mm_HandSolder | ~
 |  | C2 | 100n | Device:C | Capacitor_SMD:C_0805_2012Metric_Pad1.15x1.40mm_HandSolder | ~
 |  | C3 | 100n | Device:C | Capacitor_SMD:C_0805_2012Metric_Pad1.15x1.40mm_HandSolder | ~
 |  | C4 | 1u | Device:C | Capacitor_SMD:C_0805_2012Metric_Pad1.15x1.40mm_HandSolder | ~
 |  | C5 | 1u | Device:C | Capacitor_SMD:C_0805_2012Metric_Pad1.15x1.40mm_HandSolder | ~
 |  | C6 | 1u | Device:C | Capacitor_SMD:C_0805_2012Metric_Pad1.15x1.40mm_HandSolder | ~
 |  | C7 | 100n | Device:C | Capacitor_SMD:C_0805_2012Metric_Pad1.15x1.40mm_HandSolder | ~
 |  | C8 | 100n | Device:C | Capacitor_SMD:C_0805_2012Metric_Pad1.15x1.40mm_HandSolder | ~
 |  | C9 | 100n | Device:C | Capacitor_SMD:C_0805_2012Metric_Pad1.15x1.40mm_HandSolder | ~
 |  | C10 | 100n | Device:C | Capacitor_SMD:C_0805_2012Metric_Pad1.15x1.40mm_HandSolder | ~
 |  | C11 | 10n | Device:C | Capacitor_SMD:C_0805_2012Metric_Pad1.15x1.40mm_HandSolder | ~
 |  | C12 | 470u | Device:CP | Capacitor_SMD:CP_Elec_8x10 | ~
 |  | C13 | 470u | Device:CP | Capacitor_SMD:CP_Elec_8x10 | ~
 |  | D1 | D_SCH_1N5819 | e-Power:D_SCH_1N5819 | Diode_SMD:D_SOD-323_HandSoldering
 |  | D2 | LED | Device:LED | e-Power:LED_0805_1.15x1.40mm_HandSolder | ~
 |  | D3 | LED | Device:LED | e-Power:LED_0805_1.15x1.40mm_HandSolder | ~
 |  | D4 | LED | Device:LED | e-Power:LED_0805_1.15x1.40mm_HandSolder | ~
 |  | D5 | 1N4148 | Diode:1N4148 | e-Power:DO-35_SMD | https://assets.nexperia.com/documents/data-sheet/1N4148_1N4448.pdf
 |  | F1 | Fuse | Device:Fuse | Fuse:Fuse_0805_2012Metric_Pad1.15x1.40mm_HandSolder | ~
 |  | FB1 | Ferrite_Bead | Device:Ferrite_Bead | Ferrite_THT:LairdTech_28C0236-0JW-10 | ~
 |  | J1 | Pedal Sensor 1 | Connector_Generic:Conn_01x03 | Connector_Phoenix_GMSTB:PhoenixContact_GMSTBA_2,5_3-G_1x03_P7.50mm_Horizontal | ~
 |  | J2 | Pedal Sensor 2 | Connector_Generic:Conn_01x03 | Connector_Phoenix_GMSTB:PhoenixContact_GMSTBA_2,5_3-G_1x03_P7.50mm_Horizontal | ~
 |  | J3 | DB9_Female | Connector:DB9_Female | Connector_Dsub:DSUB-9_Female_EdgeMount_P2.77mm | ~
 |  | J4 | DB9_Female | Connector:DB9_Female | Connector_Dsub:DSUB-9_Female_EdgeMount_P2.77mm | ~
 |  | J5 | Screw_Terminal_01x02 | Connector:Screw_Terminal_01x02 | Connector_Phoenix_GMSTB:PhoenixContact_GMSTBA_2,5_2-G-7,62_1x02_P7.62mm_Horizontal | ~
 |  | J6 | Brake Sensor | Connector_Generic:Conn_01x03 | Connector_Phoenix_GMSTB:PhoenixContact_GMSTBA_2,5_3-G_1x03_P7.50mm_Horizontal | ~
 |  | K1 | DIPxx-1Cxx-51x | Relay:DIPxx-1Cxx-51x | Relay_THT:Relay_SPDT_SANYOU_SRD_Series_Form_C | https://standexelectronics.com/wp-content/uploads/datasheet_reed_relay_DIP.pdf
 |  | Q1 | BC547 | Transistor_BJT:BC547 | Package_TO_SOT_SMD:SC-59_Handsoldering | http://www.fairchildsemi.com/ds/BC/BC547.pdf
 |  | R1 | ADJ | Device:R | Resistor_SMD:R_0805_2012Metric_Pad1.15x1.40mm_HandSolder | ~
 |  | R2 | 1K2 | Device:R | Resistor_SMD:R_0805_2012Metric_Pad1.15x1.40mm_HandSolder | ~
 |  | R3 | 18K | Device:R | Resistor_SMD:R_0805_2012Metric_Pad1.15x1.40mm_HandSolder | ~
 |  | R4 | ADJ | Device:R | Resistor_SMD:R_0805_2012Metric_Pad1.15x1.40mm_HandSolder | ~
 |  | R5 | 1K2 | Device:R | Resistor_SMD:R_0805_2012Metric_Pad1.15x1.40mm_HandSolder | ~
 |  | R6 | 18K | Device:R | Resistor_SMD:R_0805_2012Metric_Pad1.15x1.40mm_HandSolder | ~
 |  | R7 | 10K | Device:R | Resistor_SMD:R_0805_2012Metric_Pad1.15x1.40mm_HandSolder | ~
 |  | R8 | 10K | Device:R | Resistor_SMD:R_0805_2012Metric_Pad1.15x1.40mm_HandSolder | ~
 |  | R9 | 10K | Device:R | Resistor_SMD:R_0805_2012Metric_Pad1.15x1.40mm_HandSolder | ~
 |  | R10 | ADJ | Device:R | Resistor_SMD:R_0805_2012Metric_Pad1.15x1.40mm_HandSolder | ~
 |  | R11 | 2K2 | Device:R | Resistor_SMD:R_0805_2012Metric_Pad1.15x1.40mm_HandSolder | ~
 |  | R12 | ADJ | Device:R | Resistor_SMD:R_0805_2012Metric_Pad1.15x1.40mm_HandSolder | ~
 |  | R13 | 2K2 | Device:R | Resistor_SMD:R_0805_2012Metric_Pad1.15x1.40mm_HandSolder | ~
 |  | R14 | 10K | Device:R | Resistor_SMD:R_0805_2012Metric_Pad1.15x1.40mm_HandSolder | ~
 |  | R15 | ADJ | Device:R | Resistor_SMD:R_0805_2012Metric_Pad1.15x1.40mm_HandSolder | ~
 |  | R16 | 10K | Device:R | Resistor_SMD:R_0805_2012Metric_Pad1.15x1.40mm_HandSolder | ~
 |  | R17 | 10K | Device:R | Resistor_SMD:R_0805_2012Metric_Pad1.15x1.40mm_HandSolder | ~
 |  | R18 | 2K7 | Device:R | Resistor_SMD:R_0805_2012Metric_Pad1.15x1.40mm_HandSolder | ~
 |  | R19 | 120 | Device:R | Resistor_SMD:R_0805_2012Metric_Pad1.15x1.40mm_HandSolder | ~
 |  | R20 | 1K | Device:R | Resistor_SMD:R_0805_2012Metric_Pad1.15x1.40mm_HandSolder | ~
 |  | R21 | 330 | Device:R | Resistor_SMD:R_0805_2012Metric_Pad1.15x1.40mm_HandSolder | ~
 |  | R22 | 330 | Device:R | Resistor_SMD:R_0805_2012Metric_Pad1.15x1.40mm_HandSolder | ~
 |  | R23 | 330 | Device:R | Resistor_SMD:R_0805_2012Metric_Pad1.15x1.40mm_HandSolder | ~
 |  | R24 | 330 | Device:R | Resistor_SMD:R_0805_2012Metric_Pad1.15x1.40mm_HandSolder | ~
 |  | R25 | 1K | Device:R | Resistor_SMD:R_0805_2012Metric_Pad1.15x1.40mm_HandSolder | ~
 |  | R26 | ADJ | Device:R | Resistor_SMD:R_0805_2012Metric_Pad1.15x1.40mm_HandSolder | ~
 |  | R27 | ADJ | Device:R | Resistor_SMD:R_0805_2012Metric_Pad1.15x1.40mm_HandSolder | ~
 |  | R28 | 2K2 | Device:R | Resistor_SMD:R_0805_2012Metric_Pad1.15x1.40mm_HandSolder | ~
 |  | R29 | ADJ | Device:R | Resistor_SMD:R_0805_2012Metric_Pad1.15x1.40mm_HandSolder | ~
 |  | R30 | 3K3 | Device:R | Resistor_SMD:R_0805_2012Metric_Pad1.15x1.40mm_HandSolder | ~
 |  | R31 | 10K | Device:R | Resistor_SMD:R_0805_2012Metric_Pad1.15x1.40mm_HandSolder | ~
 |  | U1 | LM358 | Amplifier_Operational:LM358 | e-Power:DIP-8_SMD | http://www.ti.com/lit/ds/symlink/lm2904-n.pdf
 |  | U2 | LM358 | Amplifier_Operational:LM358 | e-Power:DIP-8_SMD | http://www.ti.com/lit/ds/symlink/lm2904-n.pdf
 |  | U3 | MCP2558FD-xSN | Interface_CAN_LIN:MCP2558FD-xSN | Package_SO:SOIC-8_3.9x4.9mm_P1.27mm | https://ww1.microchip.com/downloads/en/DeviceDoc/20005533A.pdf
 |  | U4 | LM317_TO39 | Regulator_Linear:LM317_TO39 | Package_TO_SOT_THT:TO-39-3 | http://www.ti.com/lit/ds/symlink/lm317.pdf
 |  | U5 | UFRGS_PILL | e-Power:UFRGS_PILL | e-Power:UFRGS_PILL
Collated Components:
Item | Qty | Reference(s) | Value | LibPart | Footprint | Datasheet
1 | 7 | C1, C2, C3, C7, C8, C9, C10 | 100n | Device:C | Capacitor_SMD:C_0805_2012Metric_Pad1.15x1.40mm_HandSolder | ~
2 | 3 | C4, C5, C6 | 1u | Device:C | Capacitor_SMD:C_0805_2012Metric_Pad1.15x1.40mm_HandSolder | ~
3 | 1 | C11 | 10n | Device:C | Capacitor_SMD:C_0805_2012Metric_Pad1.15x1.40mm_HandSolder | ~
4 | 2 | C12, C13 | 470u | Device:CP | Capacitor_SMD:CP_Elec_8x10 | ~
5 | 1 | D1 | D_SCH_1N5819 | e-Power:D_SCH_1N5819 | Diode_SMD:D_SOD-323_HandSoldering
6 | 3 | D2, D3, D4 | LED | Device:LED | e-Power:LED_0805_1.15x1.40mm_HandSolder | ~
7 | 1 | D5 | 1N4148 | Diode:1N4148 | e-Power:DO-35_SMD | https://assets.nexperia.com/documents/data-sheet/1N4148_1N4448.pdf
8 | 1 | F1 | Fuse | Device:Fuse | Fuse:Fuse_0805_2012Metric_Pad1.15x1.40mm_HandSolder | ~
9 | 1 | FB1 | Ferrite_Bead | Device:Ferrite_Bead | Ferrite_THT:LairdTech_28C0236-0JW-10 | ~
10 | 1 | J1 | Pedal Sensor 1 | Connector_Generic:Conn_01x03 | Connector_Phoenix_GMSTB:PhoenixContact_GMSTBA_2,5_3-G_1x03_P7.50mm_Horizontal | ~
11 | 1 | J2 | Pedal Sensor 2 | Connector_Generic:Conn_01x03 | Connector_Phoenix_GMSTB:PhoenixContact_GMSTBA_2,5_3-G_1x03_P7.50mm_Horizontal | ~
12 | 2 | J3, J4 | DB9_Female | Connector:DB9_Female | Connector_Dsub:DSUB-9_Female_EdgeMount_P2.77mm | ~
13 | 1 | J5 | Screw_Terminal_01x02 | Connector:Screw_Terminal_01x02 | Connector_Phoenix_GMSTB:PhoenixContact_GMSTBA_2,5_2-G-7,62_1x02_P7.62mm_Horizontal | ~
14 | 1 | J6 | Brake Sensor | Connector_Generic:Conn_01x03 | Connector_Phoenix_GMSTB:PhoenixContact_GMSTBA_2,5_3-G_1x03_P7.50mm_Horizontal | ~
15 | 1 | K1 | DIPxx-1Cxx-51x | Relay:DIPxx-1Cxx-51x | Relay_THT:Relay_SPDT_SANYOU_SRD_Series_Form_C | https://standexelectronics.com/wp-content/uploads/datasheet_reed_relay_DIP.pdf
16 | 1 | Q1 | BC547 | Transistor_BJT:BC547 | Package_TO_SOT_SMD:SC-59_Handsoldering | http://www.fairchildsemi.com/ds/BC/BC547.pdf
17 | 8 | R1, R4, R10, R12, R15, R26, R27, R29 | ADJ | Device:R | Resistor_SMD:R_0805_2012Metric_Pad1.15x1.40mm_HandSolder | ~
18 | 2 | R2, R5 | 1K2 | Device:R | Resistor_SMD:R_0805_2012Metric_Pad1.15x1.40mm_HandSolder | ~
19 | 2 | R3, R6 | 18K | Device:R | Resistor_SMD:R_0805_2012Metric_Pad1.15x1.40mm_HandSolder | ~
20 | 7 | R7, R8, R9, R14, R16, R17, R31 | 10K | Device:R | Resistor_SMD:R_0805_2012Metric_Pad1.15x1.40mm_HandSolder | ~
21 | 3 | R11, R13, R28 | 2K2 | Device:R | Resistor_SMD:R_0805_2012Metric_Pad1.15x1.40mm_HandSolder | ~
22 | 1 | R18 | 2K7 | Device:R | Resistor_SMD:R_0805_2012Metric_Pad1.15x1.40mm_HandSolder | ~
23 | 1 | R19 | 120 | Device:R | Resistor_SMD:R_0805_2012Metric_Pad1.15x1.40mm_HandSolder | ~
24 | 2 | R20, R25 | 1K | Device:R | Resistor_SMD:R_0805_2012Metric_Pad1.15x1.40mm_HandSolder | ~
25 | 4 | R21, R22, R23, R24 | 330 | Device:R | Resistor_SMD:R_0805_2012Metric_Pad1.15x1.40mm_HandSolder | ~
26 | 1 | R30 | 3K3 | Device:R | Resistor_SMD:R_0805_2012Metric_Pad1.15x1.40mm_HandSolder | ~
27 | 2 | U1, U2 | LM358 | Amplifier_Operational:LM358 | e-Power:DIP-8_SMD | http://www.ti.com/lit/ds/symlink/lm2904-n.pdf
28 | 1 | U3 | MCP2558FD-xSN | Interface_CAN_LIN:MCP2558FD-xSN | Package_SO:SOIC-8_3.9x4.9mm_P1.27mm | https://ww1.microchip.com/downloads/en/DeviceDoc/20005533A.pdf
29 | 1 | U4 | LM317_TO39 | Regulator_Linear:LM317_TO39 | Package_TO_SOT_THT:TO-39-3 | http://www.ti.com/lit/ds/symlink/lm317.pdf
30 | 1 | U5 | UFRGS_PILL | e-Power:UFRGS_PILL | e-Power:UFRGS_PILL

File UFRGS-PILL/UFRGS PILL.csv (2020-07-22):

Source: | C:\Users\gabri\GoogleDrive\E-POWER\Eletronica\UFRGS PILL\UFRGS PILL\UFRGS PILL.sch
Date: | 7/9/2020 12:29:23 PM
Tool: | Eeschema (5.1.5)-3
Generator: | C:\Program Files\KiCad\bin\scripting\plugins/bom_csv_grouped_by_value.py
Component Count: | 38
Individual Components:
Item | Qty | Reference(s) | Value | LibPart | Footprint | Datasheet
 |  | C1 | 100nF | Device:C | Capacitor_SMD:C_0805_2012Metric_Pad1.15x1.40mm_HandSolder | ~
 |  | C2 | 100nF | Device:C | Capacitor_SMD:C_0805_2012Metric_Pad1.15x1.40mm_HandSolder | ~
 |  | C3 | 100nF | Device:C | Capacitor_SMD:C_0805_2012Metric_Pad1.15x1.40mm_HandSolder | ~
 |  | C4 | 100nF | Device:C | Capacitor_SMD:C_0805_2012Metric_Pad1.15x1.40mm_HandSolder | ~
 |  | C5 | 10uF | Device:C | Capacitor_SMD:C_0805_2012Metric_Pad1.15x1.40mm_HandSolder | ~
 |  | C6 | 100nF | Device:C | Capacitor_SMD:C_0805_2012Metric_Pad1.15x1.40mm_HandSolder | ~
 |  | C7 | 100nF | Device:C | Capacitor_SMD:C_0805_2012Metric_Pad1.15x1.40mm_HandSolder | ~
 |  | C8 | 100nF | Device:C | Capacitor_SMD:C_0805_2012Metric_Pad1.15x1.40mm_HandSolder | ~
 |  | C9 | 10uF | Device:C | Capacitor_SMD:C_0805_2012Metric_Pad1.15x1.40mm_HandSolder | ~
 |  | C10 | 10uF | Device:C | Capacitor_SMD:C_0805_2012Metric_Pad1.15x1.40mm_HandSolder | ~
 |  | C11 | 100nF | Device:C | Capacitor_SMD:C_0805_2012Metric_Pad1.15x1.40mm_HandSolder | ~
 |  | C12 | 12pF | Device:C | Capacitor_SMD:C_0805_2012Metric_Pad1.15x1.40mm_HandSolder | ~
 |  | C13 | 12pF | Device:C | Capacitor_SMD:C_0805_2012Metric_Pad1.15x1.40mm_HandSolder | ~
 |  | C14 | 100pF | Device:C | Capacitor_SMD:C_0805_2012Metric_Pad1.15x1.40mm_HandSolder | ~
 |  | C15 | 100pF | Device:C | Capacitor_SMD:C_0805_2012Metric_Pad1.15x1.40mm_HandSolder | ~
 |  | D1 | BAT54A | Diode:BAT54A | Package_TO_SOT_SMD:SOT-23 | http://www.diodes.com/_files/datasheets/ds11005.pdf
 |  | D2 | BAT54A | Diode:BAT54A | e-Power:SOT-23 | http://www.diodes.com/_files/datasheets/ds11005.pdf
 |  | D3 | GRN_LED | Device:LED | LED_SMD:LED_0805_2012Metric_Pad1.15x1.40mm_HandSolder | ~
 |  | D4 | GRN_LED | Device:LED | LED_SMD:LED_0805_2012Metric_Pad1.15x1.40mm_HandSolder | ~
 |  | D5 | GRN_LED | Device:LED | LED_SMD:LED_0805_2012Metric_Pad1.15x1.40mm_HandSolder | ~
 |  | D6 | RED_LED | Device:LED | LED_SMD:LED_0805_2012Metric_Pad1.15x1.40mm_HandSolder | ~
 |  | FB1 | Ferrite_Bead | Device:Ferrite_Bead | Resistor_SMD:R_0805_2012Metric_Pad1.15x1.40mm_HandSolder | ~
 |  | J1 | ST-LINK | Connector:Conn_01x05_Male | Connector_PinHeader_2.54mm:PinHeader_1x05_P2.54mm_Horizontal | ~
 |  | J2 | USB_B_Micro | Connector:USB_B_Micro | e-Power:USB_Micro-B_Horizontal | ~
 |  | J3 | CONN_01x20 | Connector:Conn_01x20_Male | Connector_PinHeader_2.54mm:PinHeader_1x20_P2.54mm_Vertical | ~
 |  | J4 | CONN_01x20 | Connector:Conn_01x20_Male | Connector_PinHeader_2.54mm:PinHeader_1x20_P2.54mm_Vertical | ~
 |  | R1 | 0R | Device:R | Resistor_SMD:R_0805_2012Metric_Pad1.15x1.40mm_HandSolder | ~
 |  | R2 | 0R | Device:R | Resistor_SMD:R_0805_2012Metric_Pad1.15x1.40mm_HandSolder | ~
 |  | R4 | 330R | Device:R | Resistor_SMD:R_0805_2012Metric_Pad1.15x1.40mm_HandSolder | ~
 |  | R5 | 330R | Device:R | Resistor_SMD:R_0805_2012Metric_Pad1.15x1.40mm_HandSolder | ~
 |  | R6 | 330R | Device:R | Resistor_SMD:R_0805_2012Metric_Pad1.15x1.40mm_HandSolder | ~
 |  | R7 | 330R | Device:R | Resistor_SMD:R_0805_2012Metric_Pad1.15x1.40mm_HandSolder | ~
 |  | R8 | 10K | Device:R | Resistor_SMD:R_0805_2012Metric_Pad1.15x1.40mm_HandSolder | ~
 |  | SW1 | SW_Push | Switch:SW_Push | e-Power:SW_Push_1P1T_NO_6x6mm_H9.5mm | ~
 |  | U1 | AZ1117-3.3 | Regulator_Linear:AZ1117-3.3 | Package_TO_SOT_SMD:SOT-223-3_TabPin2 | https://www.diodes.com/assets/Datasheets/AZ1117.pdf
 |  | U2 | STM32G431CBTx | e-Power:STM32G431CBTx | Package_QFP:LQFP-48_7x7mm_P0.5mm | https://www.st.com/resource/en/datasheet/stm32g431cb.pdf
 |  | Y1 | 24MHz | Device:Crystal | Crystal:Crystal_HC49-4H_Vertical | ~
 |  | Y2 | 32K768Hz | Device:Crystal | Crystal:Crystal_HC49-4H_Vertical | ~
Collated Components:
Item | Qty | Reference(s) | Value | LibPart | Footprint | Datasheet
1 | 8 | C1, C2, C3, C4, C6, C7, C8, C11 | 100nF | Device:C | Capacitor_SMD:C_0805_2012Metric_Pad1.15x1.40mm_HandSolder | ~
2 | 3 | C5, C9, C10 | 10uF | Device:C | Capacitor_SMD:C_0805_2012Metric_Pad1.15x1.40mm_HandSolder | ~
3 | 2 | C12, C13 | 12pF | Device:C | Capacitor_SMD:C_0805_2012Metric_Pad1.15x1.40mm_HandSolder | ~
4 | 2 | C14, C15 | 100pF | Device:C | Capacitor_SMD:C_0805_2012Metric_Pad1.15x1.40mm_HandSolder | ~
5 | 1 | D1 | BAT54A | Diode:BAT54A | Package_TO_SOT_SMD:SOT-23 | http://www.diodes.com/_files/datasheets/ds11005.pdf
6 | 1 | D2 | BAT54A | Diode:BAT54A | e-Power:SOT-23 | http://www.diodes.com/_files/datasheets/ds11005.pdf
7 | 3 | D3, D4, D5 | GRN_LED | Device:LED | LED_SMD:LED_0805_2012Metric_Pad1.15x1.40mm_HandSolder | ~
8 | 1 | D6 | RED_LED | Device:LED | LED_SMD:LED_0805_2012Metric_Pad1.15x1.40mm_HandSolder | ~
9 | 1 | FB1 | Ferrite_Bead | Device:Ferrite_Bead | Resistor_SMD:R_0805_2012Metric_Pad1.15x1.40mm_HandSolder | ~
10 | 1 | J1 | ST-LINK | Connector:Conn_01x05_Male | Connector_PinHeader_2.54mm:PinHeader_1x05_P2.54mm_Horizontal | ~
11 | 1 | J2 | USB_B_Micro | Connector:USB_B_Micro | e-Power:USB_Micro-B_Horizontal | ~
12 | 2 | J3, J4 | CONN_01x20 | Connector:Conn_01x20_Male | Connector_PinHeader_2.54mm:PinHeader_1x20_P2.54mm_Vertical | ~
13 | 2 | R1, R2 | 0R | Device:R | Resistor_SMD:R_0805_2012Metric_Pad1.15x1.40mm_HandSolder | ~
14 | 4 | R4, R5, R6, R7 | 330R | Device:R | Resistor_SMD:R_0805_2012Metric_Pad1.15x1.40mm_HandSolder | ~
15 | 1 | R8 | 10K | Device:R | Resistor_SMD:R_0805_2012Metric_Pad1.15x1.40mm_HandSolder | ~
16 | 1 | SW1 | SW_Push | Switch:SW_Push | e-Power:SW_Push_1P1T_NO_6x6mm_H9.5mm | ~
17 | 1 | U1 | AZ1117-3.3 | Regulator_Linear:AZ1117-3.3 | Package_TO_SOT_SMD:SOT-223-3_TabPin2 | https://www.diodes.com/assets/Datasheets/AZ1117.pdf
18 | 1 | U2 | STM32G431CBTx | e-Power:STM32G431CBTx | Package_QFP:LQFP-48_7x7mm_P0.5mm | https://www.st.com/resource/en/datasheet/stm32g431cb.pdf
19 | 1 | Y1 | 24MHz | Device:Crystal | Crystal:Crystal_HC49-4H_Vertical | ~
20 | 1 | Y2 | 32K768Hz | Device:Crystal | Crystal:Crystal_HC49-4H_Vertical | ~

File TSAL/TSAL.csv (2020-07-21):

Source: | C:\Users\gabri\GoogleDrive\E-POWER\Eletronica\TSAL\TSAL - KiCad\TSAL.sch
Date: | 7/3/2020 1:07:26 AM
Tool: | Eeschema (5.1.5)-3
Generator: | C:\Program Files\KiCad\bin\scripting\plugins/bom_csv_grouped_by_value.py
Component Count: | 55
Individual Components:
Item | Qty | Reference(s) | Value | LibPart | Footprint | Datasheet | Color | Comment | Loops | Power | Size | Voltage
 |  | C1 | 100uF | Device:CP | Capacitor_THT:C_Radial_D8.0mm_H11.5mm_P3.50mm | ~ |  |  |  |  |  | 16V
 |  | C2 | 220pF | Device:C | Capacitor_SMD:C_0805_2012Metric_Pad1.15x1.40mm_HandSolder | ~
 |  | C3 | 100uF | Device:CP | Capacitor_THT:C_Radial_D8.0mm_H11.5mm_P3.50mm | ~ |  |  |  |  |  | 16V
 |  | C4 | 100nF | Device:C | Capacitor_SMD:C_0805_2012Metric_Pad1.15x1.40mm_HandSolder | ~
 |  | C5 | 1uF | Device:CP | Capacitor_THT:C_Radial_D6.3mm_H11.0mm_P2.50mm | ~ |  |  |  |  |  | 16V
 |  | C6 | 100nF | Device:C | Capacitor_SMD:C_0805_2012Metric_Pad1.15x1.40mm_HandSolder | ~
 |  | C7 | 100nF | Device:C | Capacitor_SMD:C_0805_2012Metric_Pad1.15x1.40mm_HandSolder | ~
 |  | D1 | 1N4747A | Diode:1N47xxA | Diode_THT:D_DO-41_SOD81_P10.16mm_Horizontal | https://www.vishay.com/docs/85816/1n4728a.pdf |  |  |  | 1.3W |  | 20V
 |  | D2 | 1N4747A | Diode:1N47xxA | Diode_THT:D_DO-41_SOD81_P10.16mm_Horizontal | https://www.vishay.com/docs/85816/1n4728a.pdf |  |  |  | 1.3W |  | 20V
 |  | D3 | 1N5819 | Diode:1N5819 | Diode_THT:D_DO-41_SOD81_P10.16mm_Horizontal | http://www.vishay.com/docs/88525/1n5817.pdf
 |  | D4 | 1N5819 | Diode:1N5819 | Diode_THT:D_DO-41_SOD81_P10.16mm_Horizontal | http://www.vishay.com/docs/88525/1n5817.pdf
 |  | D5 | LED | Device:LED | LED_SMD:LED_0805_2012Metric | ~ | GREEN |  |  |  | 5mm
 |  | D6 | LED | Device:LED | LED_SMD:LED_0805_2012Metric | ~ | RED |  |  |  | 5mm
 |  | D7 | RGB LED | Device:LED_ABRG | Connector_Phoenix_GMSTB:PhoenixContact_GMSTBA_2,5_4-G_1x04_P7.50mm_Horizontal | ~ |  |  |  | 50W
 |  | G1 | UFRGS_1_14.7x8.0mm_Copper | e-Power:UFRGS_1_14.7x8.0mm_Copper | e-Power:UFRGS_14.7x8.0mm_Copper
 |  | G2 | e-Power_16.5x8.0mm_Copper-e-Power | TSAL-rescue:e-Power_16.5x8.0mm_Copper-e-Power-e-Power | e-Power:e-Power_16.5x8.0mm_Copper
 |  | J1 | Screw_Terminal_01x02 | Connector:Screw_Terminal_01x02 | Connector_Phoenix_GMSTB:PhoenixContact_GMSTBA_2,5_2-G-7,62_1x02_P7.62mm_Horizontal | ~ |  | Tractive System Voltage
 |  | K1 | FINDER-32.21-x000 | Relay:FINDER-32.21-x000 | Relay_THT:Relay_SPDT_SANYOU_SRD_Series_Form_C | https://gfinder.findernet.com/assets/Series/355/S32EN.pdf
 |  | L1 | 170uH | pspice:INDUCTOR | Inductor_THT:L_Toroid_Horizontal_D28.0mm_P26.67mm_Bourns_2200 | ~ |  |  | 50 TURNS
 |  | Q1 | BC548 | Transistor_BJT:BC548 | Package_TO_SOT_THT:TO-92_Inline | http://www.fairchildsemi.com/ds/BC/BC547.pdf
 |  | Q2 | IRF3205 | Transistor_FET:IRF3205 | Package_TO_SOT_THT:TO-220-3_Horizontal_TabDown | http://www.irf.com/product-info/datasheets/data/irf3205.pdf
 |  | Q3 | IRF3205 | Transistor_FET:IRF3205 | Package_TO_SOT_THT:TO-220-3_Horizontal_TabDown | http://www.irf.com/product-info/datasheets/data/irf3205.pdf
 |  | R1 | 10K | Device:R | Resistor_SMD:R_0805_2012Metric_Pad1.15x1.40mm_HandSolder | ~
 |  | R2 | 0.68R | Device:R | Resistor_SMD:R_0805_2012Metric_Pad1.15x1.40mm_HandSolder | ~
 |  | R3 | 4K7R | Device:R | Resistor_THT:R_Axial_DIN0617_L17.0mm_D6.0mm_P25.40mm_Horizontal | ~ |  |  |  | 5W
 |  | R4 | 4K7R | Device:R | Resistor_THT:R_Axial_DIN0617_L17.0mm_D6.0mm_P25.40mm_Horizontal | ~ |  |  |  | 5W
 |  | R5 | 4K7R | Device:R | Resistor_THT:R_Axial_DIN0617_L17.0mm_D6.0mm_P25.40mm_Horizontal | ~ |  |  |  | 5W
 |  | R6 | 4K7R | Device:R | Resistor_THT:R_Axial_DIN0617_L17.0mm_D6.0mm_P25.40mm_Horizontal | ~ |  |  |  | 5W
 |  | R7 | 100R | Device:R | Resistor_SMD:R_0805_2012Metric_Pad1.15x1.40mm_HandSolder | ~
 |  | R8 | 10K | Device:R | Resistor_SMD:R_0805_2012Metric_Pad1.15x1.40mm_HandSolder | ~
 |  | R9 | 10K | Device:R | Resistor_SMD:R_0805_2012Metric_Pad1.15x1.40mm_HandSolder | ~
 |  | R10 | 18K | Device:R | Resistor_SMD:R_0805_2012Metric_Pad1.15x1.40mm_HandSolder | ~
 |  | R11 | 1K | Device:R | Resistor_SMD:R_0805_2012Metric_Pad1.15x1.40mm_HandSolder | ~
 |  | R12 | 1K | Device:R | Resistor_SMD:R_0805_2012Metric_Pad1.15x1.40mm_HandSolder | ~
 |  | R13 | 10K | Device:R | Resistor_SMD:R_0805_2012Metric_Pad1.15x1.40mm_HandSolder | ~
 |  | R14 | 220K | Device:R | Resistor_SMD:R_0805_2012Metric_Pad1.15x1.40mm_HandSolder | ~
 |  | R15 | 1K | Device:R | Resistor_SMD:R_0805_2012Metric_Pad1.15x1.40mm_HandSolder | ~
 |  | R16 | 1K | Device:R | Resistor_SMD:R_0805_2012Metric_Pad1.15x1.40mm_HandSolder | ~
 |  | R17 | 1K | Device:R | Resistor_SMD:R_0805_2012Metric_Pad1.15x1.40mm_HandSolder | ~
 |  | R18 | 1K | Device:R | Resistor_SMD:R_0805_2012Metric_Pad1.15x1.40mm_HandSolder | ~
 |  | R19 | 10K | Device:R | Resistor_SMD:R_0805_2012Metric_Pad1.15x1.40mm_HandSolder | ~
 |  | R20 | 10K | Device:R | Resistor_SMD:R_0805_2012Metric_Pad1.15x1.40mm_HandSolder | ~
 |  | R21 | 1K | Device:R | Resistor_SMD:R_0805_2012Metric_Pad1.15x1.40mm_HandSolder | ~
 |  | R22 | 1K | Device:R | Resistor_SMD:R_0805_2012Metric_Pad1.15x1.40mm_HandSolder | ~
 |  | R23 | 1K | Device:R | Resistor_SMD:R_0805_2012Metric_Pad1.15x1.40mm_HandSolder | ~
 |  | R24 | 1K | Device:R | Resistor_SMD:R_0805_2012Metric_Pad1.15x1.40mm_HandSolder | ~
 |  | R25 | 22R | Device:R | Resistor_SMD:R_0805_2012Metric_Pad1.15x1.40mm_HandSolder | ~ |  |  |  | 1W
 |  | R26 | 27R | Device:R | Resistor_SMD:R_0805_2012Metric_Pad1.15x1.40mm_HandSolder | ~ |  |  |  | 1W
 |  | R27 | 10K | Device:R | Resistor_SMD:R_0805_2012Metric_Pad1.15x1.40mm_HandSolder | ~
 |  | U1 | MC34063AP | Regulator_Switching:MC34063AP | Package_DIP:DIP-8_W7.62mm | http://www.onsemi.com/pub_link/Collateral/MC34063A-D.PDF
 |  | U2 | TLP290-4 | e-Power:TLP290-4 | e-Power:TLP290-4 | https://www.mouser.com/datasheet/2/408/TLP290-4-1209274.pdf
 |  | U3 | LM555 | Timer:LM555 | Package_DIP:DIP-8_W7.62mm_LongPads | http://www.ti.com/lit/ds/symlink/lm555.pdf
 |  | U4 | TL431D | Reference_Voltage:TL431D | Package_SO:SOIC-8_3.9x4.9mm_P1.27mm | http://www.ti.com/lit/ds/symlink/tl431.pdf
 |  | U5 | TL431D | Reference_Voltage:TL431D | Package_SO:SOIC-8_3.9x4.9mm_P1.27mm | http://www.ti.com/lit/ds/symlink/tl431.pdf
 |  | U6 | LM324A | Amplifier_Operational:LM324A | Package_DIP:DIP-14_W7.62mm_LongPads | http://www.ti.com/lit/ds/symlink/lm2902-n.pdf
Collated Components:
Item | Qty | Reference(s) | Value | LibPart | Footprint | Datasheet | Color | Comment | Loops | Power | Size | Voltage
1 | 2 | C1, C3 | 100uF | Device:CP | Capacitor_THT:C_Radial_D8.0mm_H11.5mm_P3.50mm | ~ |  |  |  |  |  | 16V
2 | 1 | C2 | 220pF | Device:C | Capacitor_SMD:C_0805_2012Metric_Pad1.15x1.40mm_HandSolder | ~
3 | 3 | C4, C6, C7 | 100nF | Device:C | Capacitor_SMD:C_0805_2012Metric_Pad1.15x1.40mm_HandSolder | ~
4 | 1 | C5 | 1uF | Device:CP | Capacitor_THT:C_Radial_D6.3mm_H11.0mm_P2.50mm | ~ |  |  |  |  |  | 16V
5 | 2 | D1, D2 | 1N4747A | Diode:1N47xxA | Diode_THT:D_DO-41_SOD81_P10.16mm_Horizontal | https://www.vishay.com/docs/85816/1n4728a.pdf |  |  |  | 1.3W |  | 20V
6 | 2 | D3, D4 | 1N5819 | Diode:1N5819 | Diode_THT:D_DO-41_SOD81_P10.16mm_Horizontal | http://www.vishay.com/docs/88525/1n5817.pdf
7 | 2 | D5, D6 | LED | Device:LED | LED_SMD:LED_0805_2012Metric | ~ | GREEN |  |  |  | 5mm
8 | 1 | D7 | RGB LED | Device:LED_ABRG | Connector_Phoenix_GMSTB:PhoenixContact_GMSTBA_2,5_4-G_1x04_P7.50mm_Horizontal | ~ |  |  |  | 50W
9 | 1 | G1 | UFRGS_1_14.7x8.0mm_Copper | e-Power:UFRGS_1_14.7x8.0mm_Copper | e-Power:UFRGS_14.7x8.0mm_Copper
10 | 1 | G2 | e-Power_16.5x8.0mm_Copper-e-Power | TSAL-rescue:e-Power_16.5x8.0mm_Copper-e-Power-e-Power | e-Power:e-Power_16.5x8.0mm_Copper
11 | 1 | J1 | Screw_Terminal_01x02 | Connector:Screw_Terminal_01x02 | Connector_Phoenix_GMSTB:PhoenixContact_GMSTBA_2,5_2-G-7,62_1x02_P7.62mm_Horizontal | ~ |  | Tractive System Voltage
12 | 1 | K1 | FINDER-32.21-x000 | Relay:FINDER-32.21-x000 | Relay_THT:Relay_SPDT_SANYOU_SRD_Series_Form_C | https://gfinder.findernet.com/assets/Series/355/S32EN.pdf
13 | 1 | L1 | 170uH | pspice:INDUCTOR | Inductor_THT:L_Toroid_Horizontal_D28.0mm_P26.67mm_Bourns_2200 | ~ |  |  | 50 TURNS
14 | 1 | Q1 | BC548 | Transistor_BJT:BC548 | Package_TO_SOT_THT:TO-92_Inline | http://www.fairchildsemi.com/ds/BC/BC547.pdf
15 | 2 | Q2, Q3 | IRF3205 | Transistor_FET:IRF3205 | Package_TO_SOT_THT:TO-220-3_Horizontal_TabDown | http://www.irf.com/product-info/datasheets/data/irf3205.pdf
16 | 7 | R1, R8, R9, R13, R19, R20, R27 | 10K | Device:R | Resistor_SMD:R_0805_2012Metric_Pad1.15x1.40mm_HandSolder | ~
17 | 1 | R2 | 0.68R | Device:R | Resistor_SMD:R_0805_2012Metric_Pad1.15x1.40mm_HandSolder | ~
18 | 4 | R3, R4, R5, R6 | 4K7R | Device:R | Resistor_THT:R_Axial_DIN0617_L17.0mm_D6.0mm_P25.40mm_Horizontal | ~ |  |  |  | 5W
19 | 1 | R7 | 100R | Device:R | Resistor_SMD:R_0805_2012Metric_Pad1.15x1.40mm_HandSolder | ~
20 | 1 | R10 | 18K | Device:R | Resistor_SMD:R_0805_2012Metric_Pad1.15x1.40mm_HandSolder | ~
21 | 10 | R11, R12, R15, R16, R17, R18, R21, R22, R23, R24 | 1K | Device:R | Resistor_SMD:R_0805_2012Metric_Pad1.15x1.40mm_HandSolder | ~
22 | 1 | R14 | 220K | Device:R | Resistor_SMD:R_0805_2012Metric_Pad1.15x1.40mm_HandSolder | ~
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

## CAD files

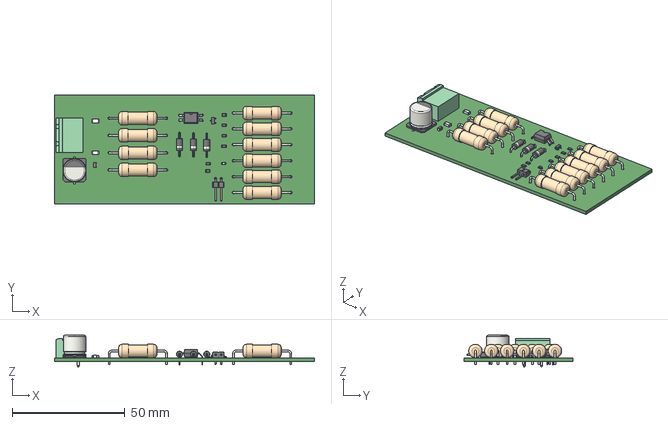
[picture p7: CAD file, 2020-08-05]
AIL/3D/AIL.step
115.5 x 48.6 x 14.0 mm

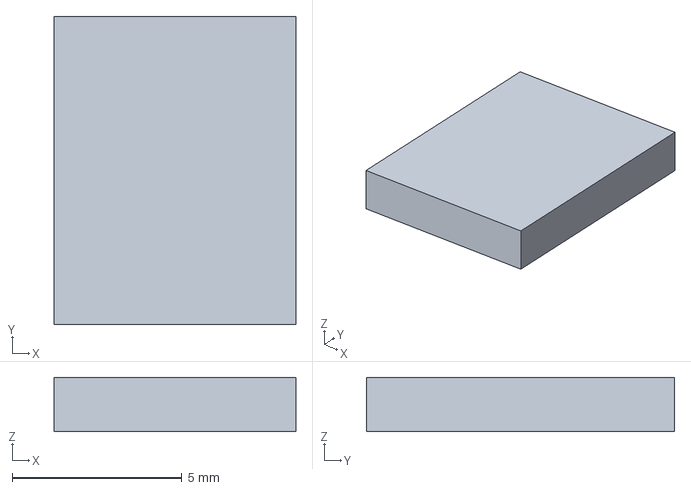
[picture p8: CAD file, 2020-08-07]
LM235_BRD/LM235_MOUNT_(sem o sensor).step
7.11 x 9.07 x 1.60 mm

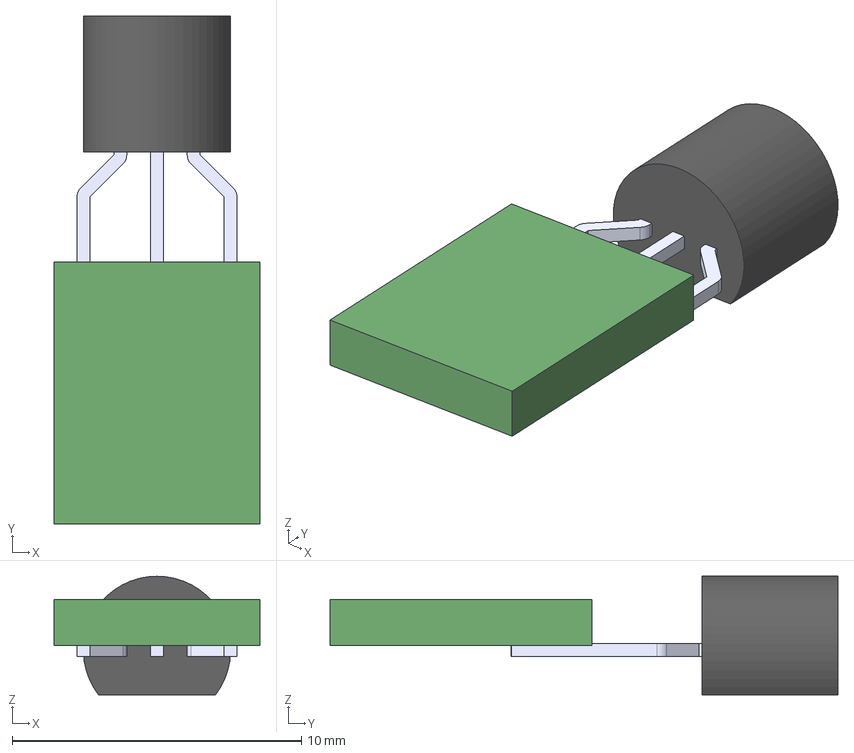
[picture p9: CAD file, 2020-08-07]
LM235_BRD/LM235_MOUNT.step
7.11 x 17.6 x 4.10 mm

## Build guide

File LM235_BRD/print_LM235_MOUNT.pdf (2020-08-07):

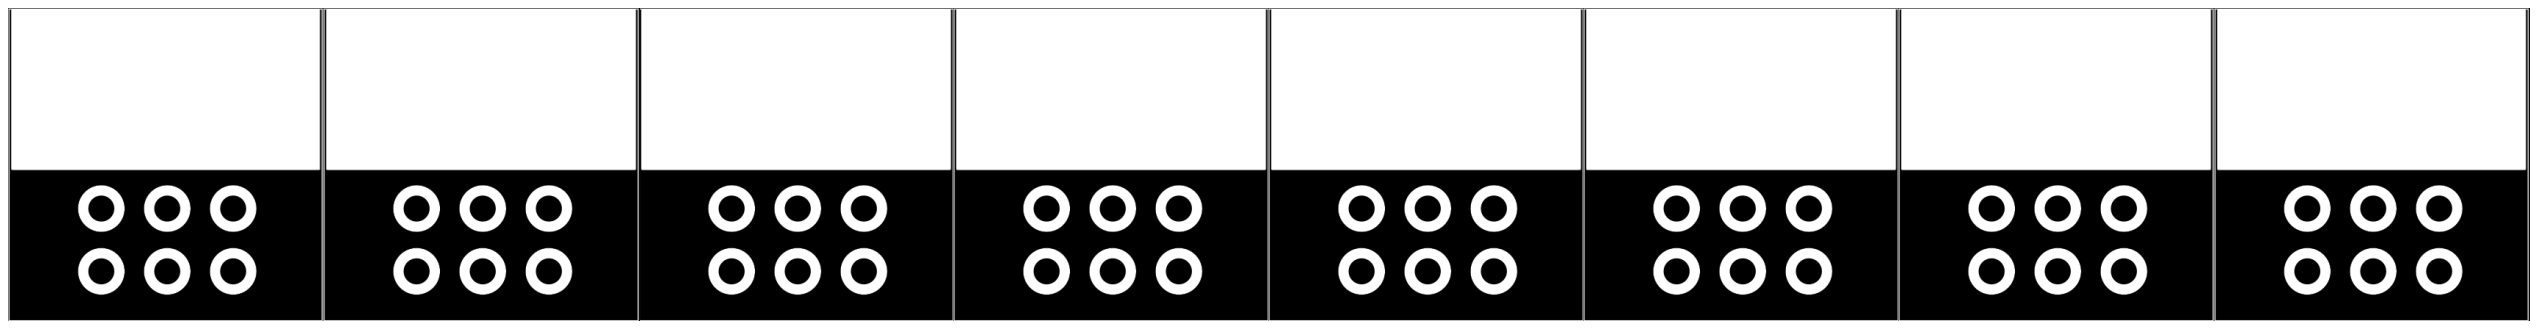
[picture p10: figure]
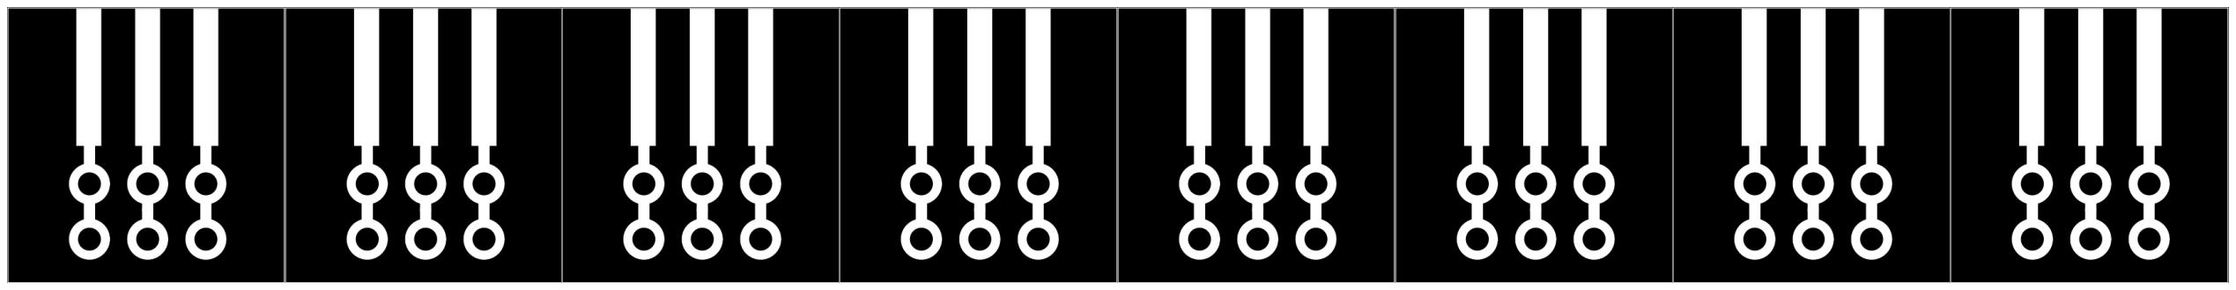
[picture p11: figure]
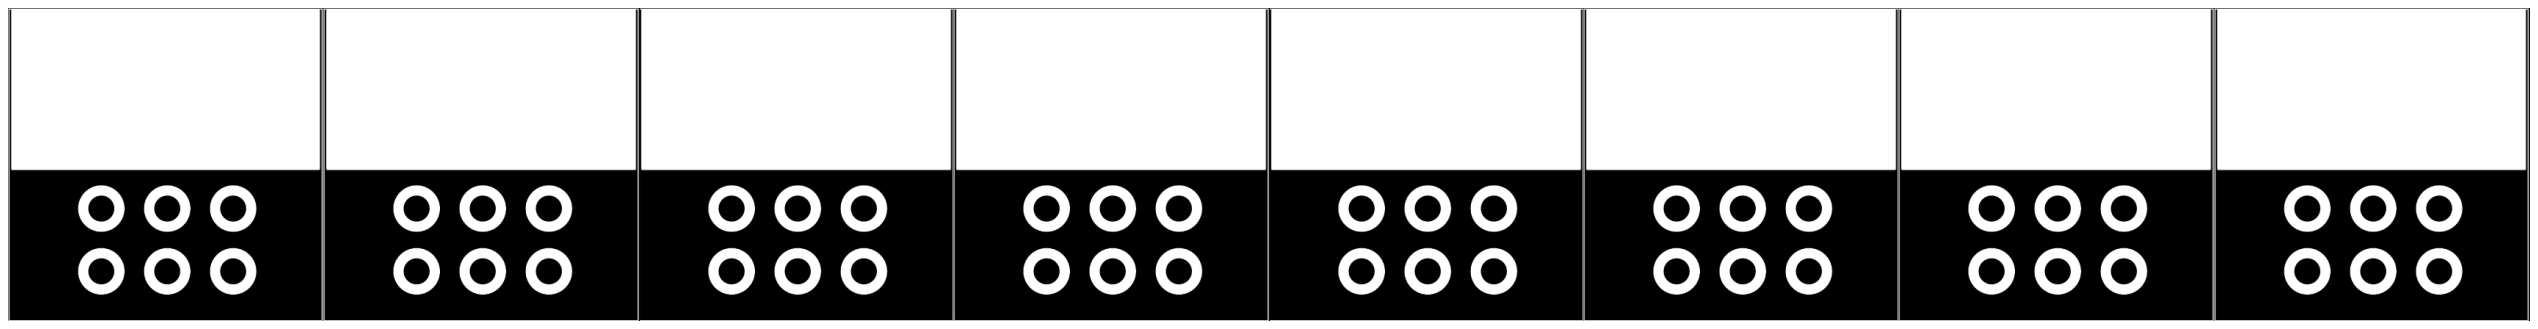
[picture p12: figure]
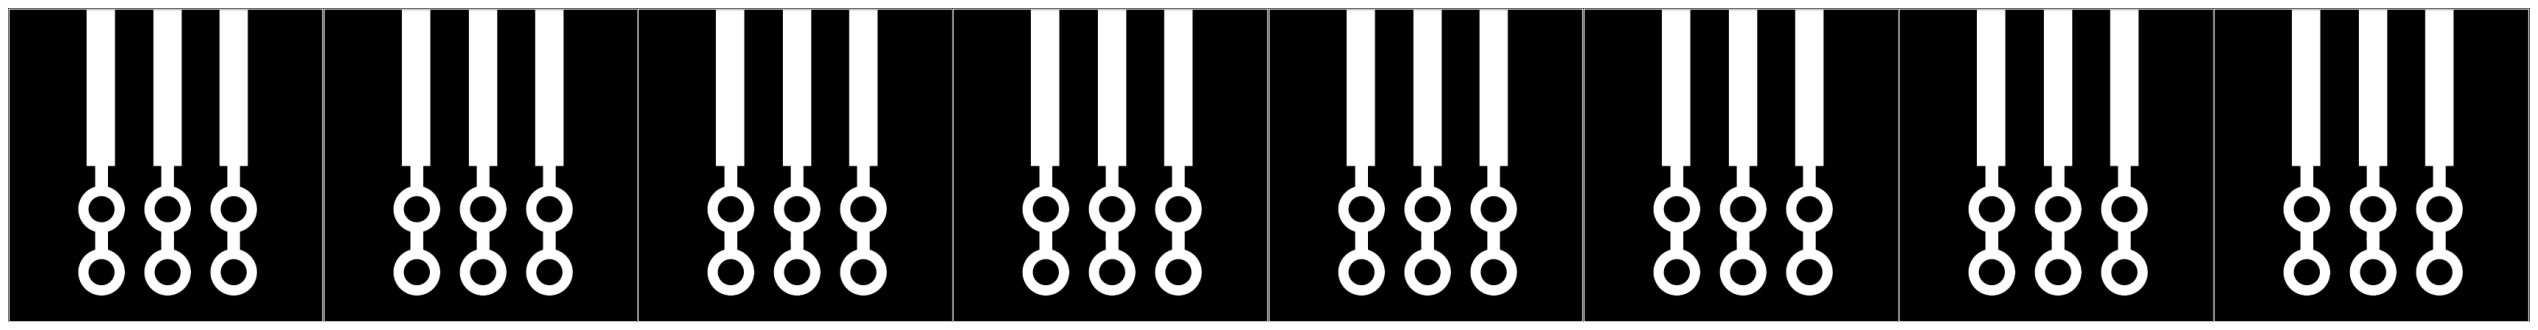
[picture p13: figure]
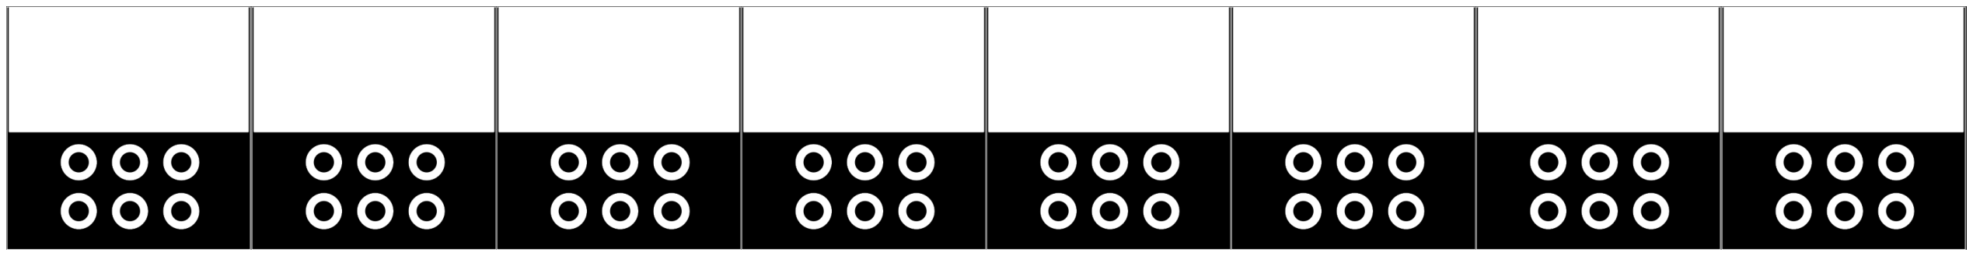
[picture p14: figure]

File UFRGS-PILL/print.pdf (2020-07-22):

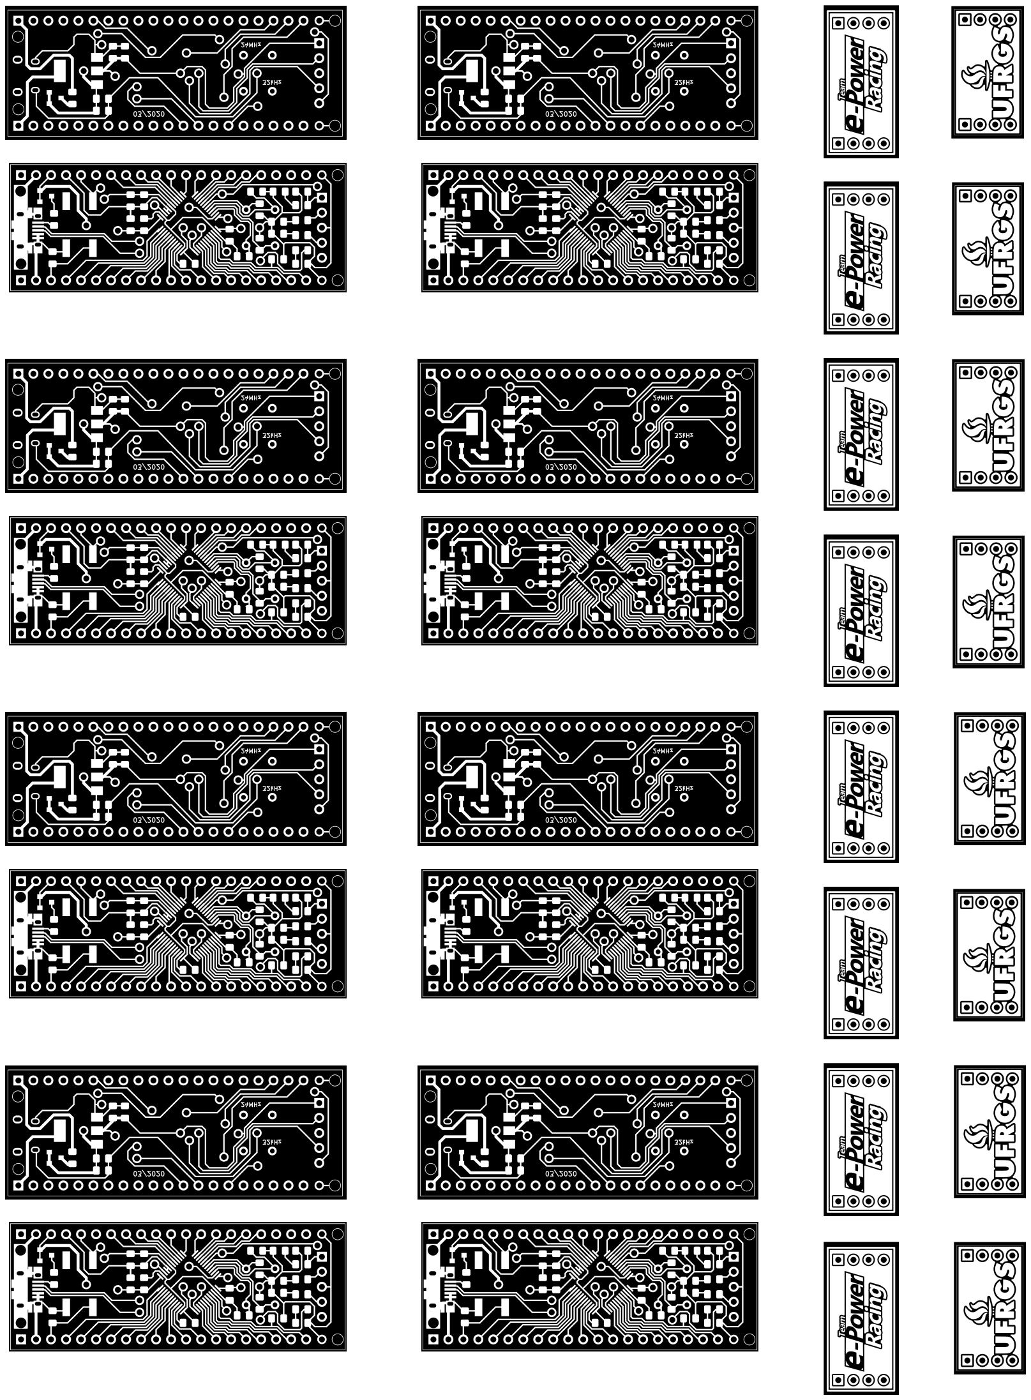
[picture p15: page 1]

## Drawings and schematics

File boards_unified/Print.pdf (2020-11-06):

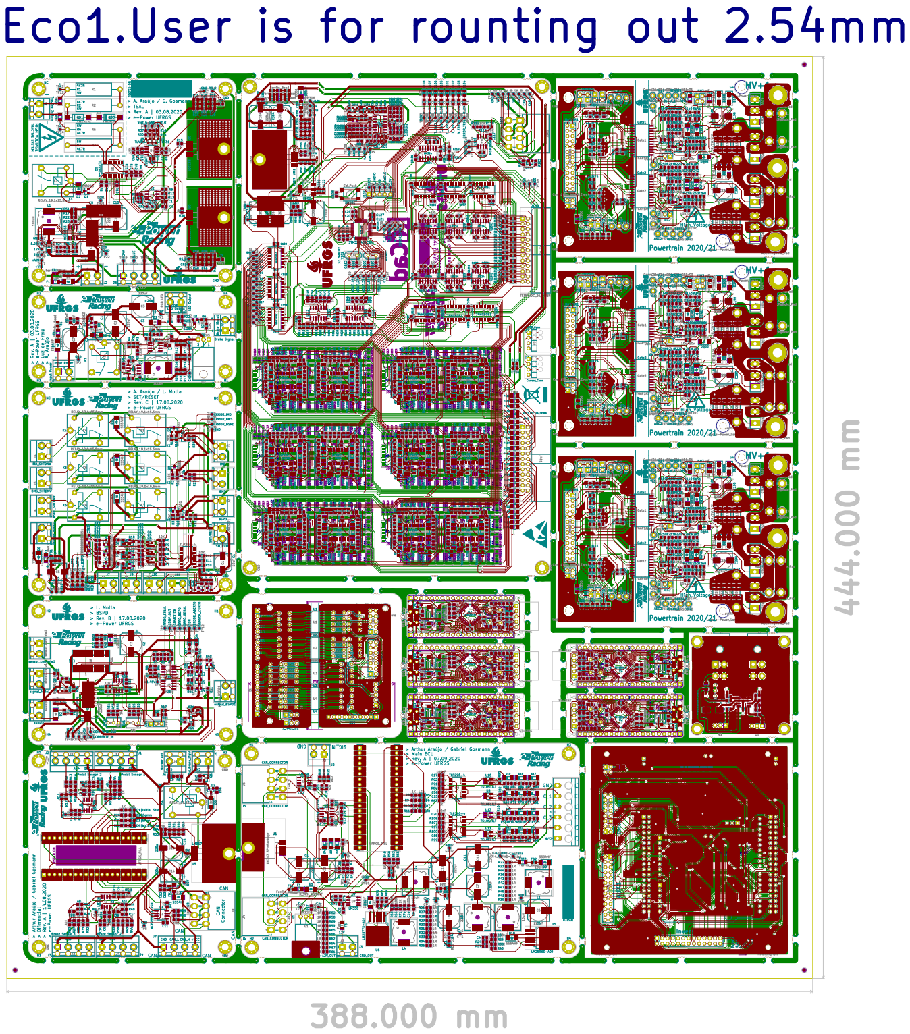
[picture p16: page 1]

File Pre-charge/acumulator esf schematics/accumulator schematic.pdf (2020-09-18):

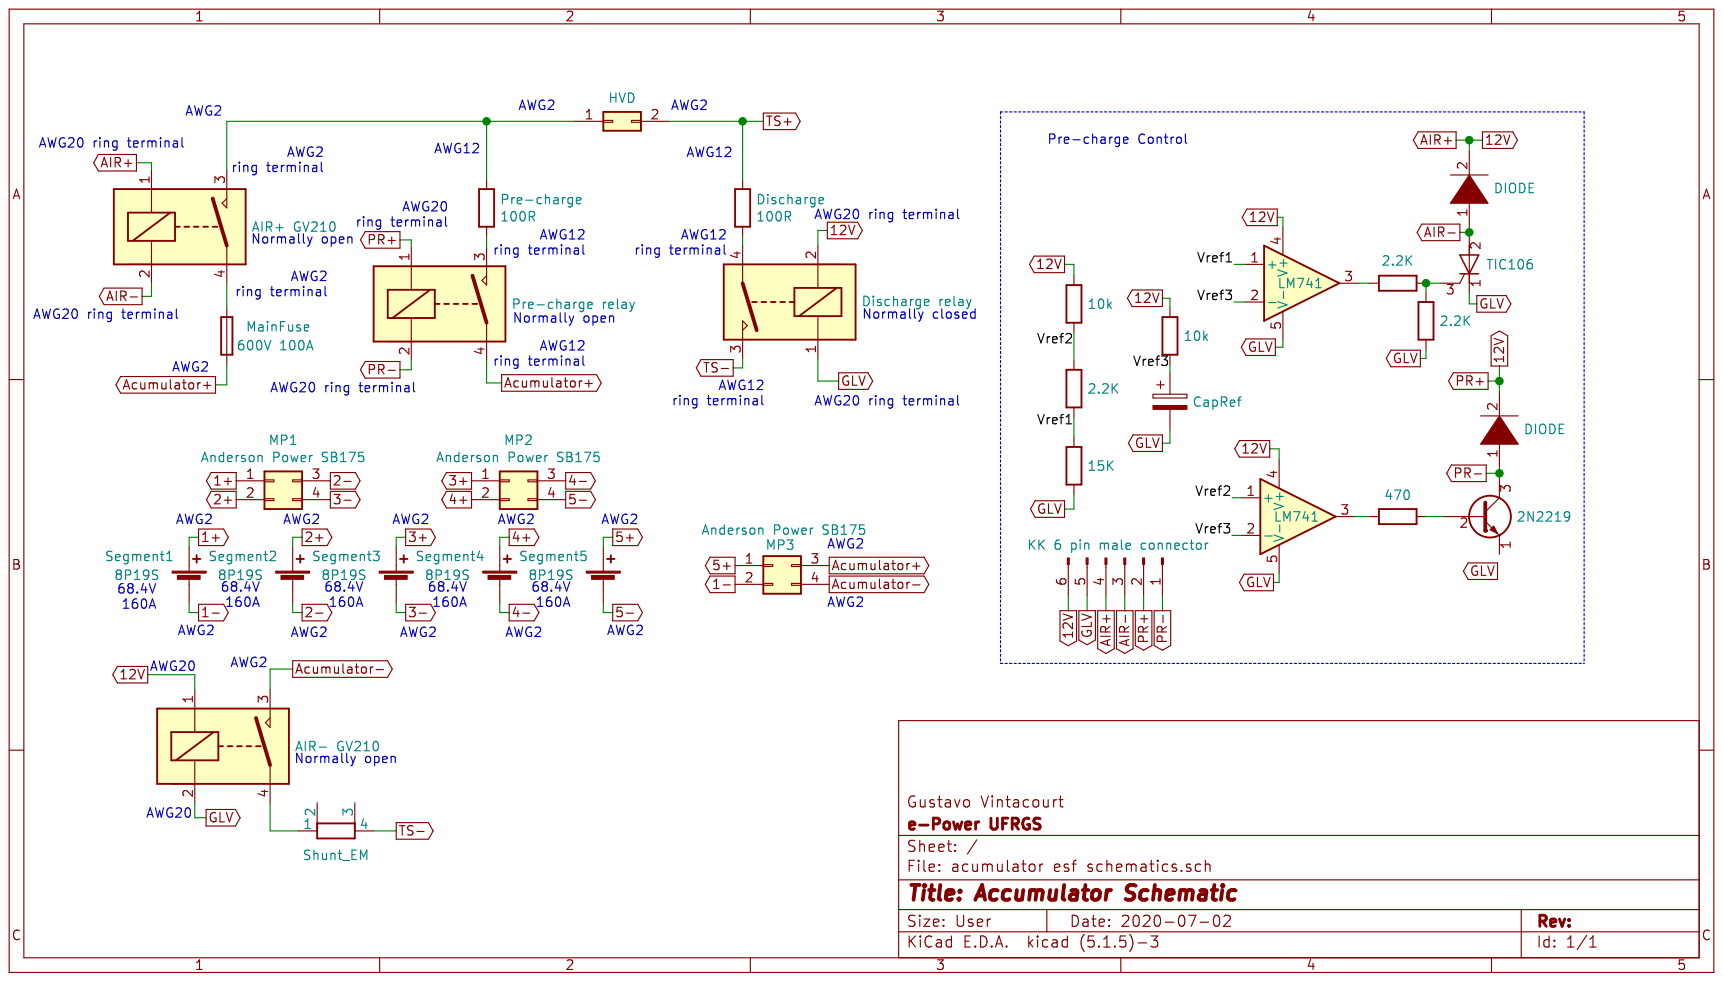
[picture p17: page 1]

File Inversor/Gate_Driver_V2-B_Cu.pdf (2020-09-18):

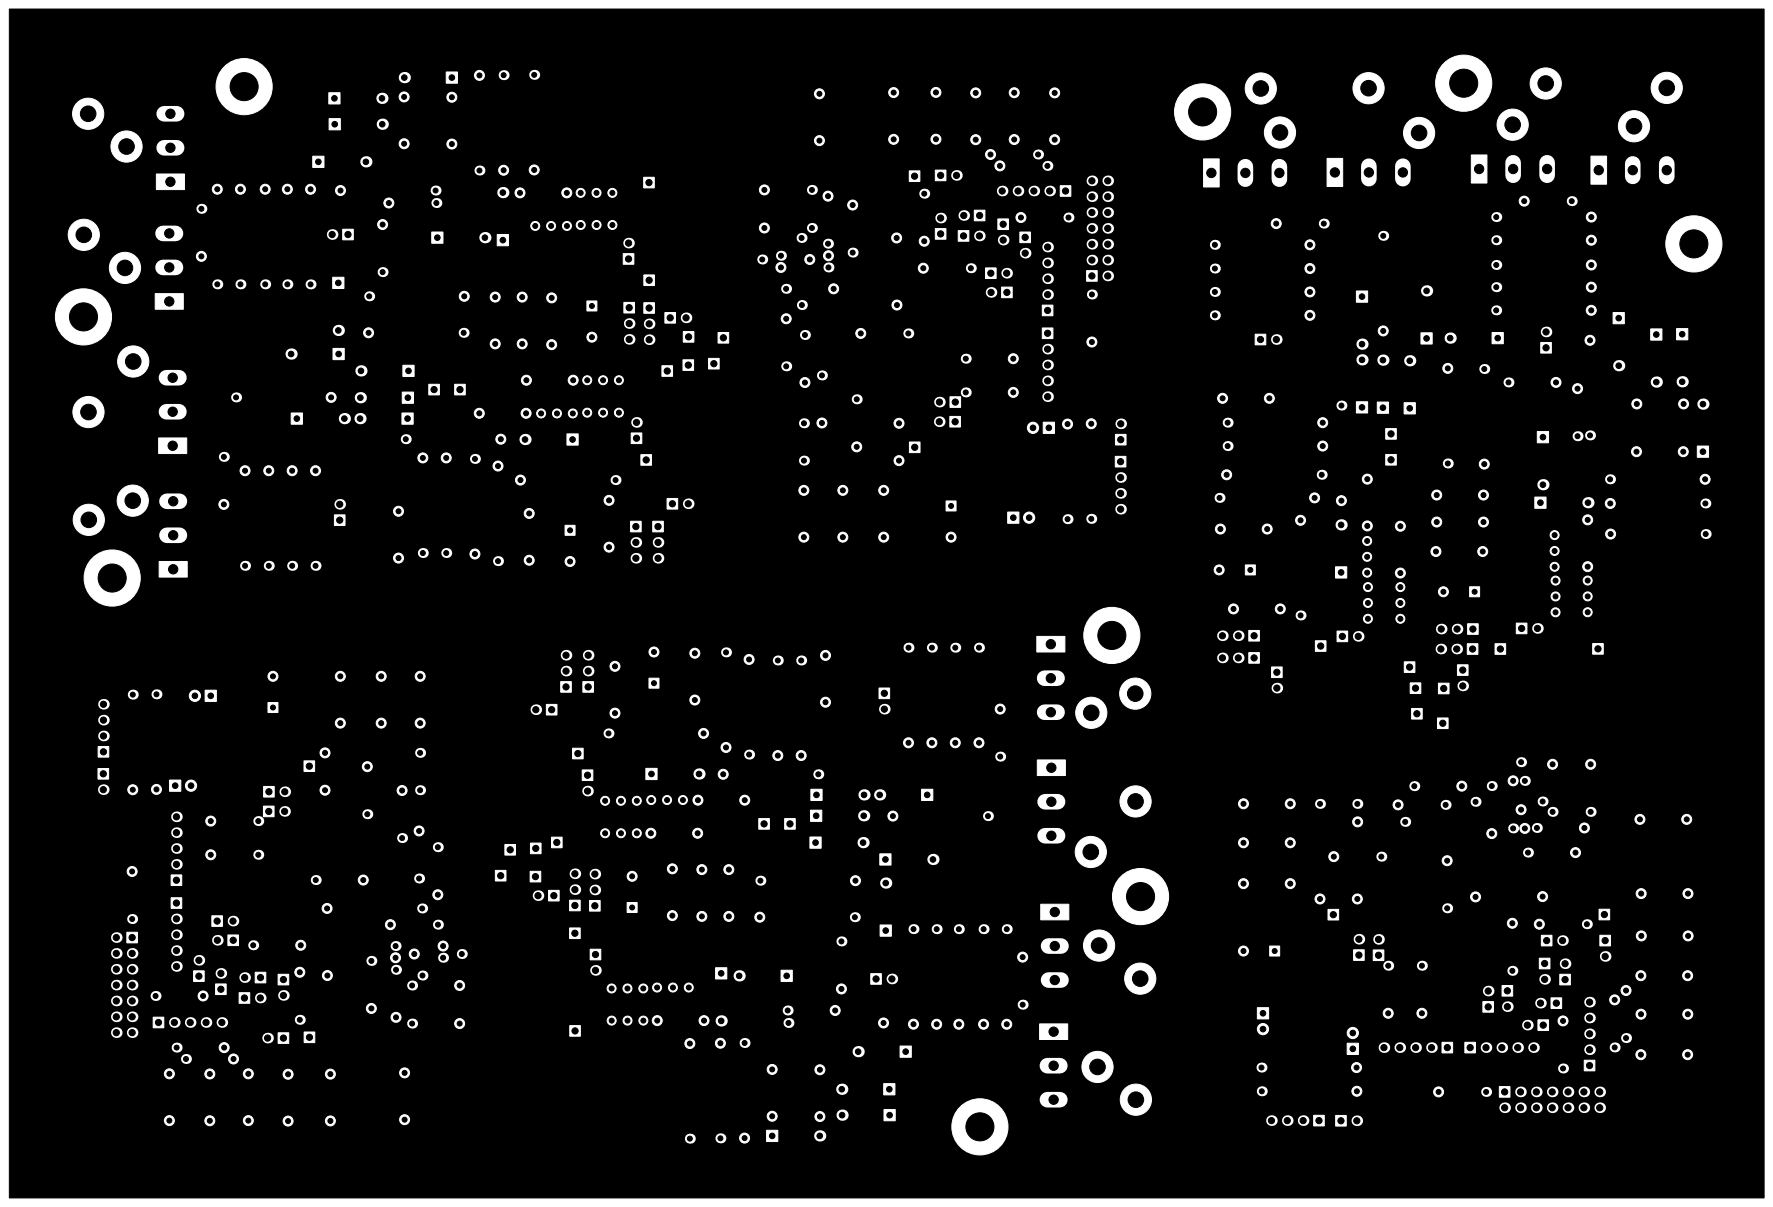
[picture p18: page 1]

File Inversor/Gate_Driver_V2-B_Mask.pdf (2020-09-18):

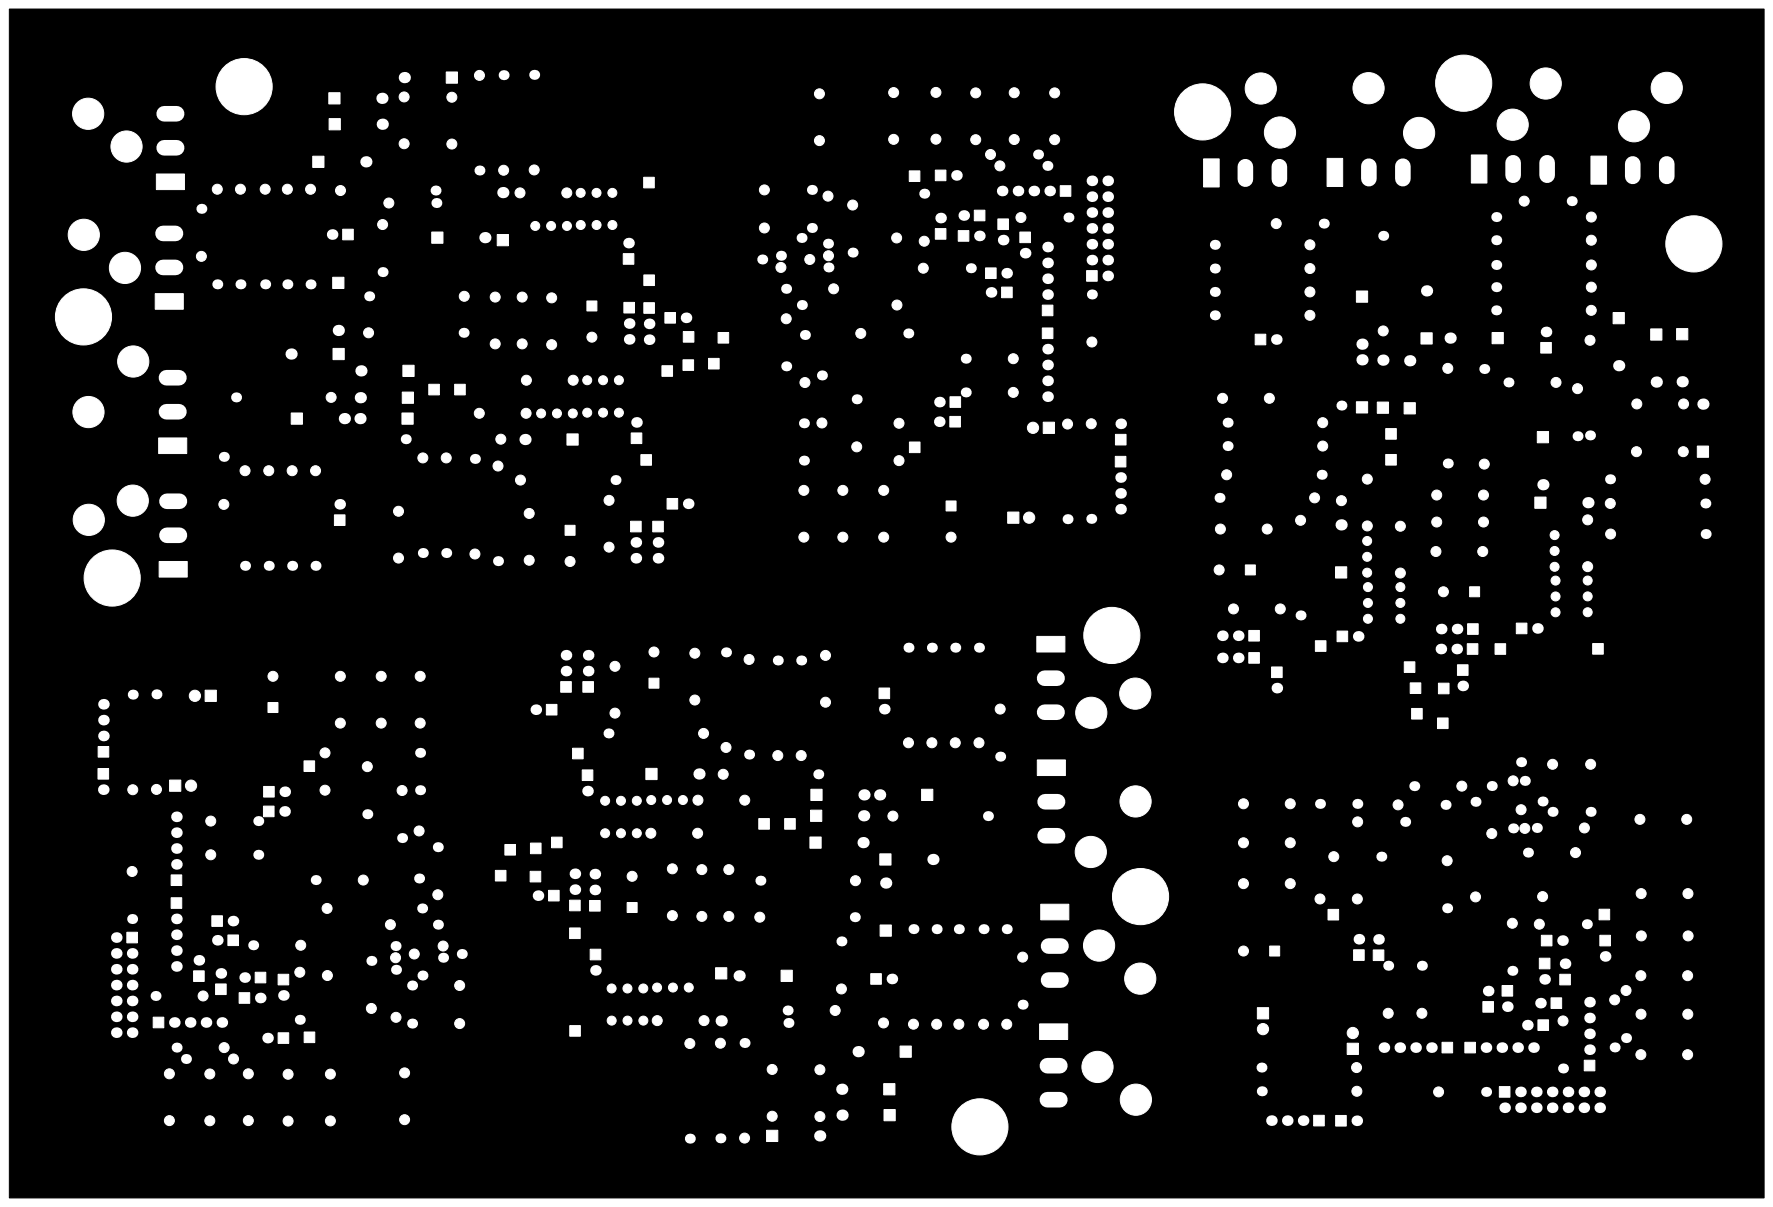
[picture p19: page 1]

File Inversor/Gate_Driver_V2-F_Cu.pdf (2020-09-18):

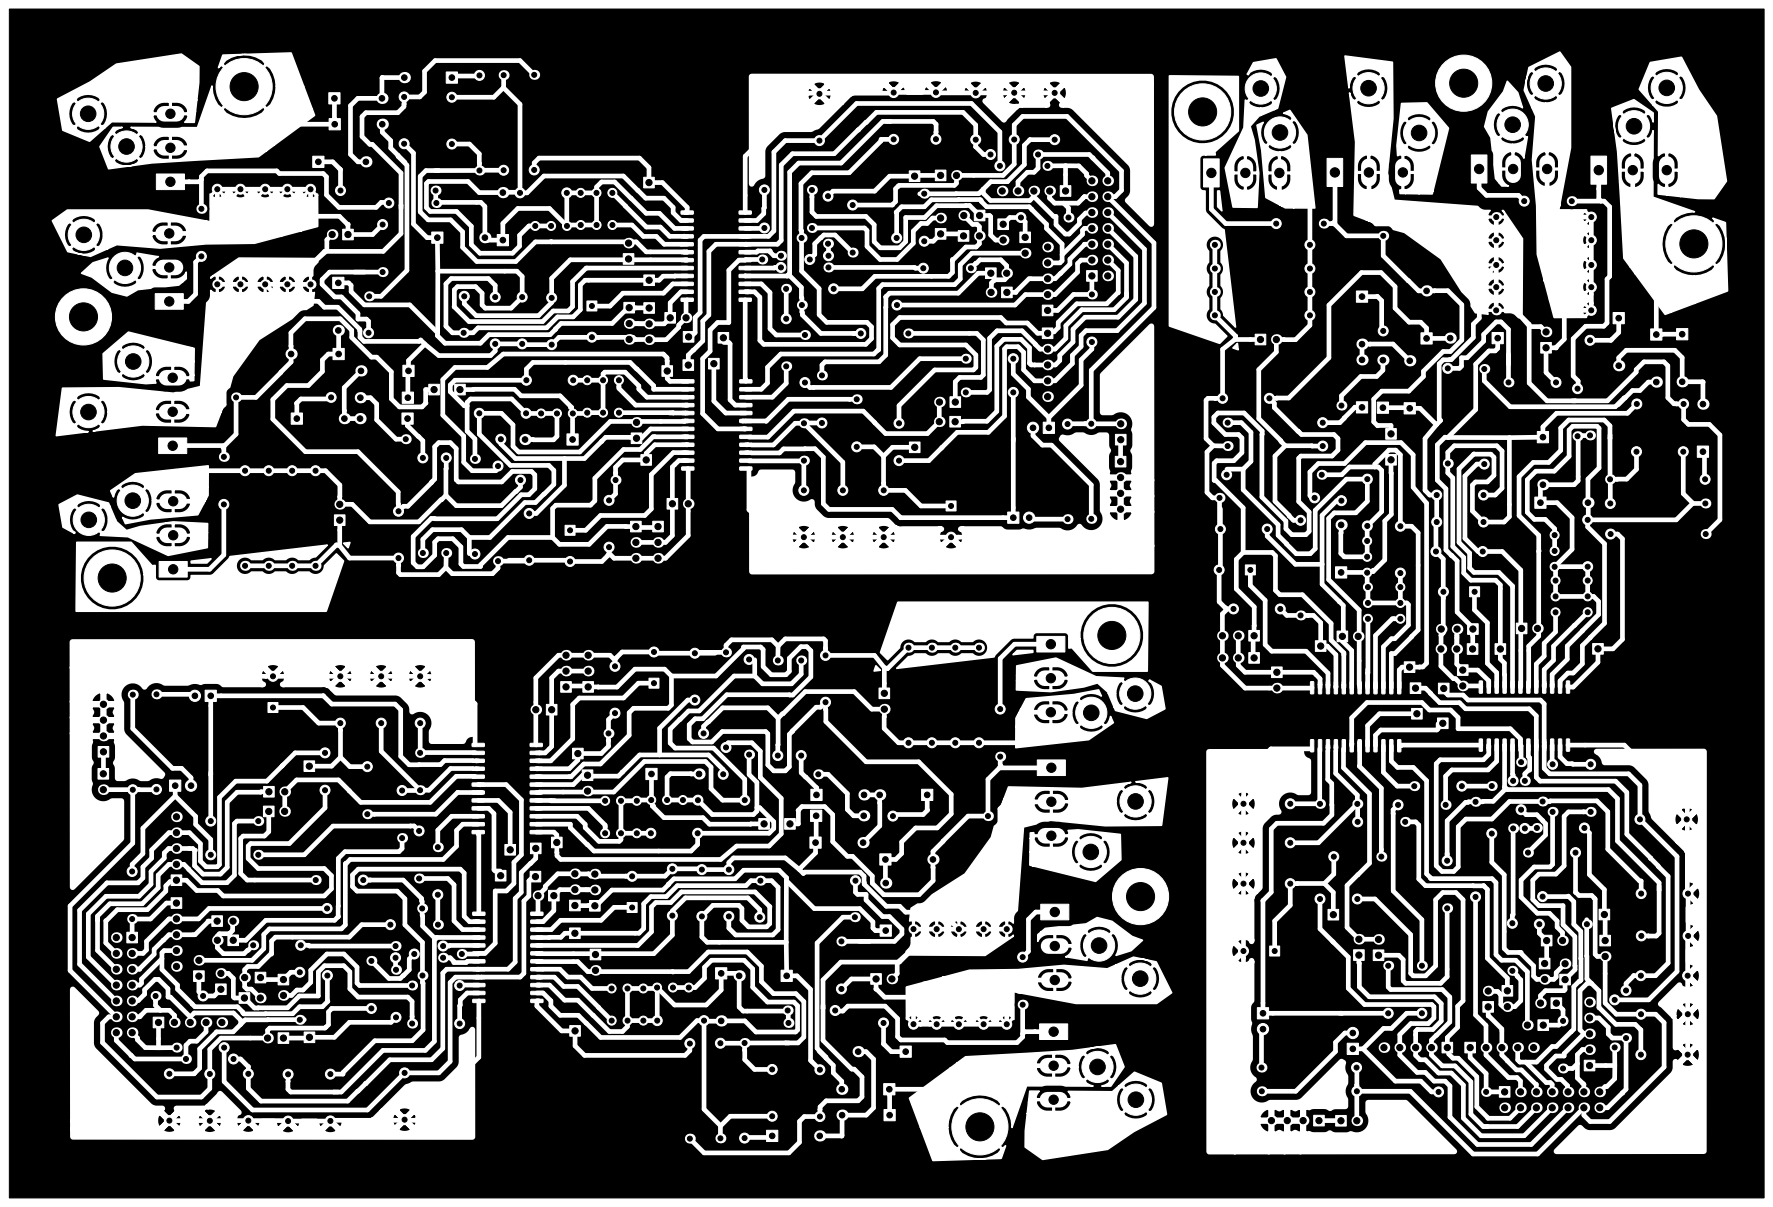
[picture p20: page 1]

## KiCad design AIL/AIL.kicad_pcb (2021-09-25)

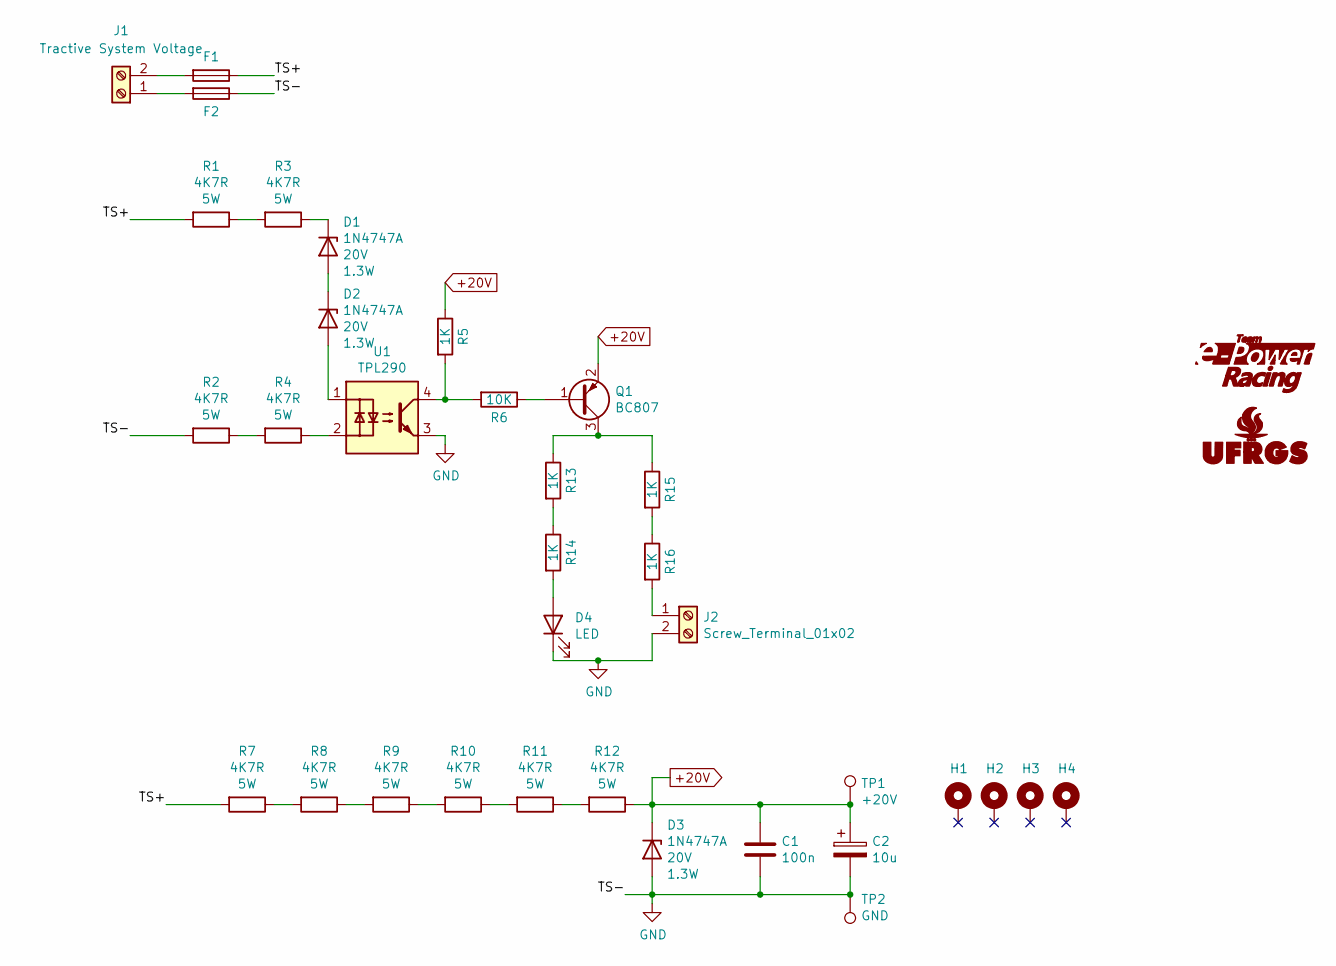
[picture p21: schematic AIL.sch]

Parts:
C1: 100n; C_0805_2012Metric
C2: 10u; CP_Elec_8x10
D1, D2, D3: 1N4747A; DO-35_SMD; Voltage 20V
D4: LED; LED_0805_1.15x1.40mm_HandSolder
F1, F2: Fuse_1206; FUSE_1206_3216Metric
G1: Logo_e-Power_Large; Logo_e-Power_16.5x8.0mm_SilkS
G2: Logo_UFRGS_Large; Logo_UFRGS_14.7x8.0mm_SilkS
H1, H2, H3, H4: NC; MountingHole_3.2mm_M3_Pad_Via
J1, J2: Screw_Terminal_01x02; TerminalBlock_Phoenix_MKDS-1,5-2_1x02_P5.08mm_Horizontal
Q1: BC807; SOT-23
R1, R2, R3, R4, R7, R8, R9, R10, R11, R12: 4K7R; R_Axial_DIN0617_L17.0mm_D6.0mm_P25.40mm_Horizontal
R5, R13, R14, R15, R16: 1K; R_0805_2012Metric_Pad1.15x1.40mm_HandSolder
R6: 10K; R_0805_2012Metric_Pad1.15x1.40mm_HandSolder
TP1: +20V; TestPoint_Pad_D1.0mm
TP2: GND; TestPoint_Pad_D1.0mm
U1: TPL290; DIP-4_W10.16mm

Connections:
+20V: C1.1, C2.1, D3.1 (K), Q1.2 (E), R5.1, R12.1, TP1.1
/TS+: F1.1, R1.2, R7.2
GND: C1.2, C2.2, D3.2 (A), D4.1 (K), F2.1, J2.2, R2.2, TP2.1, U1.3
unnamed: D1.1 (K), R3.1
unnamed: D1.2 (A), D2.1 (K)
unnamed: D2.2 (A), U1.1
unnamed: D4.2 (A), R14.2
unnamed: F1.2, J1.2
unnamed: F2.2, J1.1
unnamed: J2.1, R16.2
unnamed: Q1.1 (B), R6.1
unnamed: Q1.3 (C), R13.1, R15.1
unnamed: R1.1, R3.2
unnamed: R2.1, R4.2
unnamed: R4.1, U1.2
unnamed: R5.2, R6.2, U1.4
unnamed: R7.1, R8.2
unnamed: R8.1, R9.2
unnamed: R10.1, R11.2
unnamed: R9.1, R10.2
unnamed: R11.1, R12.2
unnamed: R13.2, R14.1
unnamed: R15.2, R16.1

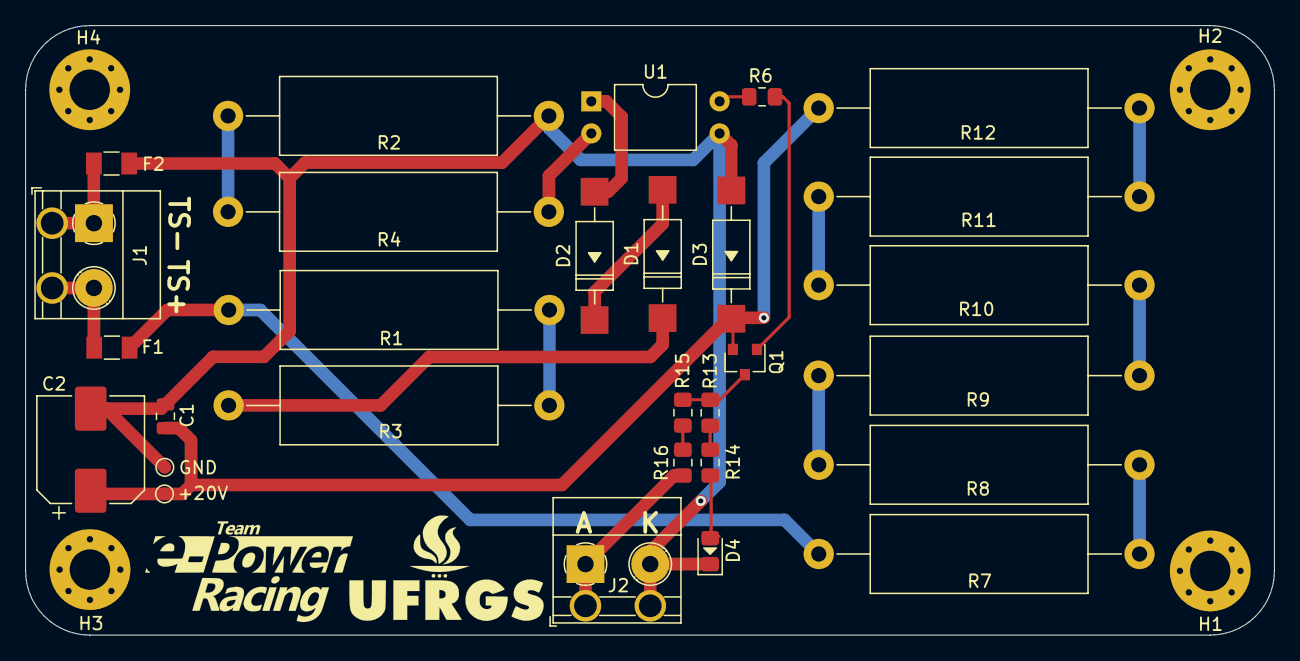
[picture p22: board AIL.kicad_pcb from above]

Board: 2 copper layers, 98.9 x 48.3 mm, 35 parts (0 on the bottom side), 23 nets.

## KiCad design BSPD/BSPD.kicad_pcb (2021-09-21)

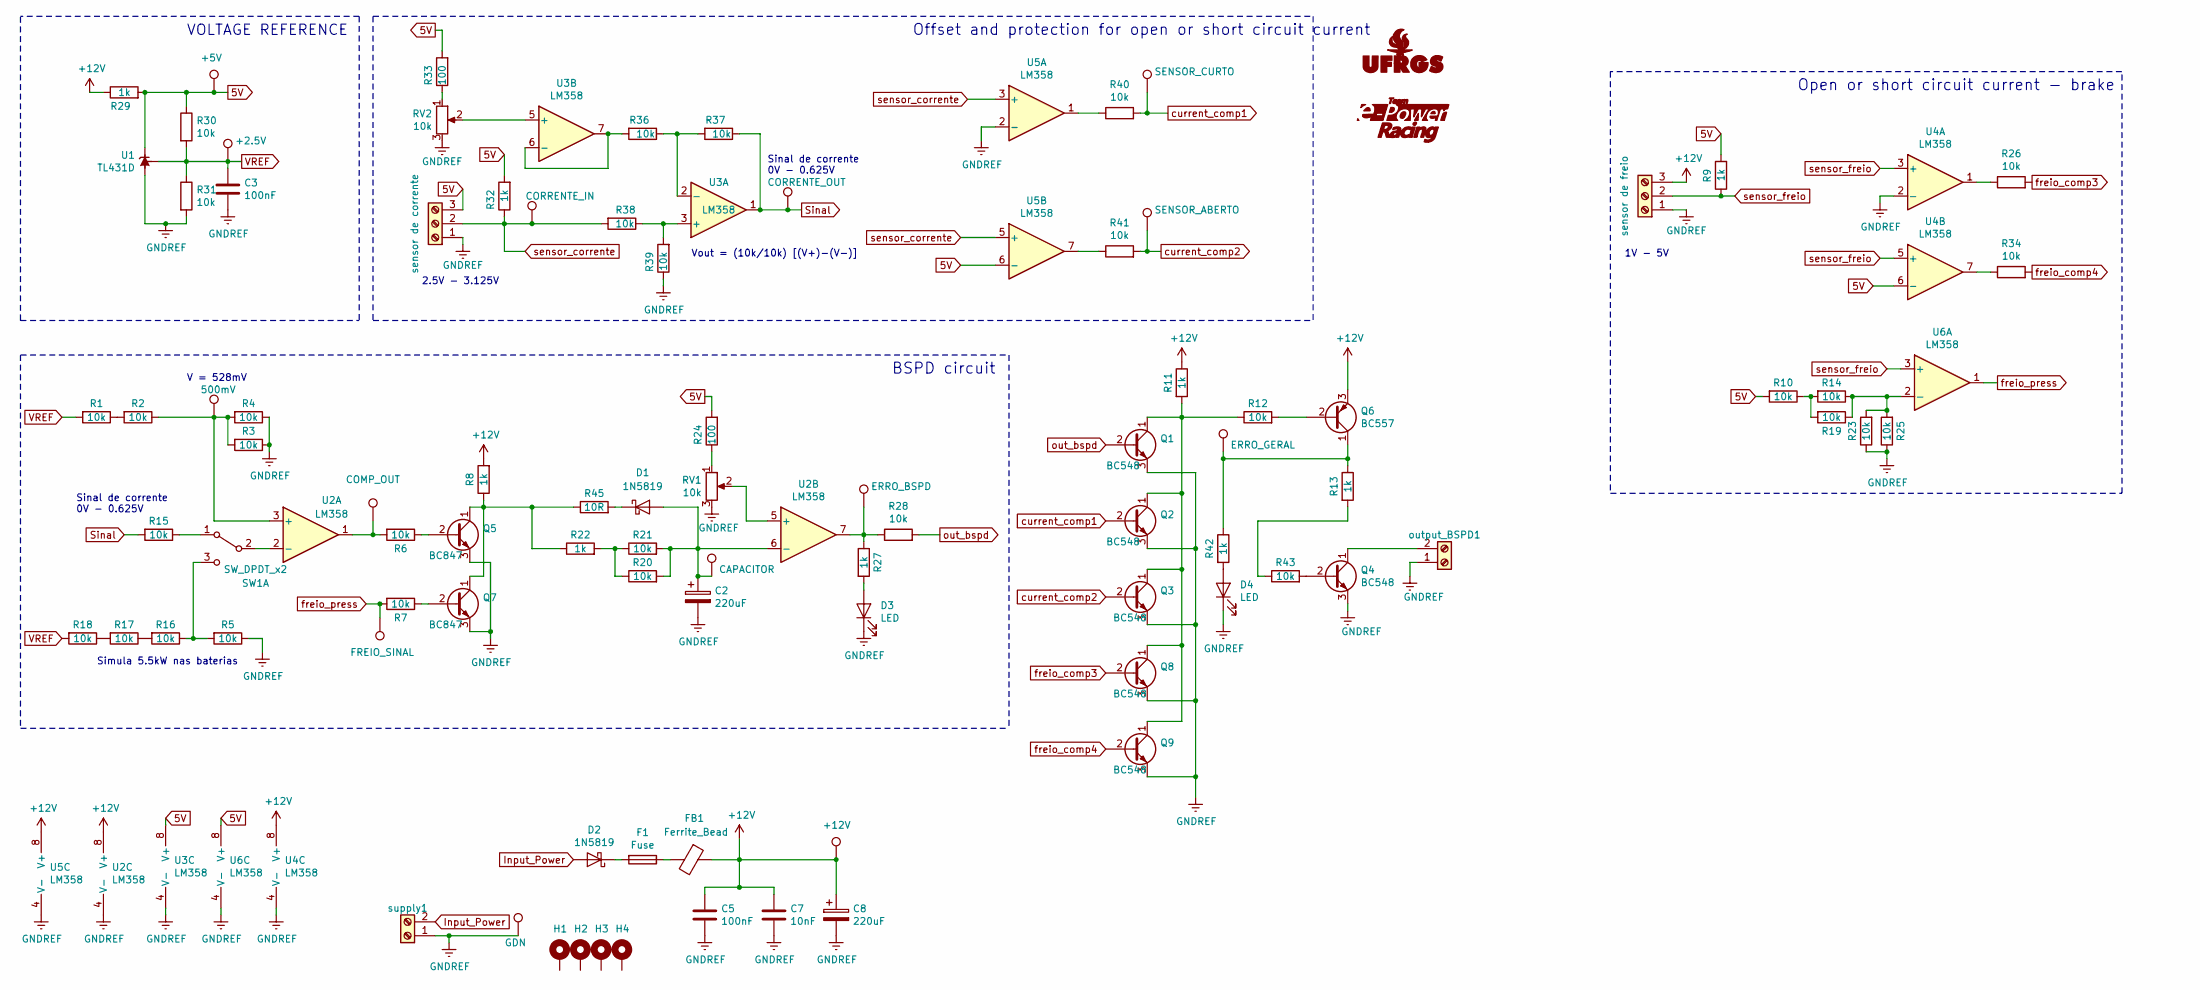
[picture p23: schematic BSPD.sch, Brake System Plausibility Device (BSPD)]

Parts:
C2, C8: 220uF; CP_Elec_10x10
C3, C5: 100nF; C_0805_2012Metric
C7: 10nF; C_0805_2012Metric
D1, D2: 1N5819; DO-214AC
D3, D4: LED; LED_0805_1.15x1.40mm_HandSolder
F1: Fuse; Fuse_0805_2012Metric
FB1: Ferrite_Bead; FB_0603_1608Metric
G1: Logo_UFRGS_Large; Logo_UFRGS_14.7x8.0mm_SilkS
G2: Logo_e-Power_Large; Logo_e-Power_16.5x8.0mm_SilkS
H1, H2, H3, H4: MountingHole_Pad; MountingHole_3.2mm_M3_Pad_Via
J1: sensor de corrente; TerminalBlock_Phoenix_MKDS-1,5-3_1x03_P5.00mm_Horizontal
Q1, Q2, Q3, Q4, Q8, Q9: BC548; SOT-23
Q5, Q7: BC847; SOT-23
Q6: BC557; SOT-23
R1, R2, R3, R4, R5, R6, R7, R10, R12, R14, R15, R16, R17, R18, R19, R20, R21, R23, R25, R26, R28, R30, R31, R34, R36, R37, R38, R39, R40, R41, R43: 10k; R_0805_2012Metric
R8, R9, R11, R13, R22, R27, R29, R32, R42: 1k; R_0805_2012Metric
R24, R33: 100; R_0805_2012Metric
R45: 10R; R_0805_2012Metric
RV1, RV2: 10k; Potentiometer_Bourns_3266Y_Vertical
SW1: SW_DPDT_x2; PinHeader_1x03_P2.54mm_Vertical
TP1: +5V; TestPoint_Pad_D1.0mm
TP2: 500mV; TestPoint_Pad_D1.0mm
TP3: +2.5V; TestPoint_Pad_D1.0mm
TP4: GDN; TestPoint_Pad_D1.0mm
TP5: CORRENTE_IN; TestPoint_Pad_D1.0mm
TP6: CORRENTE_OUT; TestPoint_Pad_D1.0mm
TP7: +12V; TestPoint_Pad_D1.0mm
TP8: COMP_OUT; TestPoint_Pad_D1.0mm
TP9: FREIO_SINAL; TestPoint_Pad_D1.0mm
TP10: CAPACITOR; TestPoint_Pad_D1.0mm
TP11: ERRO_BSPD; TestPoint_Pad_D1.0mm
TP12: SENSOR_CURTO; TestPoint_Pad_D1.0mm
TP13: SENSOR_ABERTO; TestPoint_Pad_D1.0mm
TP14: ERRO_GERAL; TestPoint_Pad_D1.0mm
U1: TL431D; SOT-23
U2, U3, U4, U5, U6: LM358; SOIC-8_3.9x4.9mm_P1.27mm
output_BSPD1: Screw_Terminal_01x02; TerminalBlock_Phoenix_MKDS-1,5-2_1x02_P5.08mm_Horizontal
sensor_freio1: sensor de freio; TerminalBlock_Phoenix_MKDS-1,5-3_1x03_P5.00mm_Horizontal
supply1: Screw_Terminal_01x02; TerminalBlock_Phoenix_MKDS-1,5-2_1x02_P5.08mm_Horizontal

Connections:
5V: J1.3, R9.2, R10.2, R24.2, R29.2, R30.1, R32.2, R33.2, TP1.1, U1.1 (K), U3.8 (V+), U4.6 (-), U5.6 (-), U6.8 (V+)
+12V: C5.1, C7.1, C8.1, FB1.1, Q6.3 (E), R8.2, R11.1, R29.1, TP7.1, U2.8 (V+), U4.8 (V+), U5.8 (V+), sensor_freio1.3; also elsewhere on the board
Input_Power: D2.2 (A), supply1.2; also elsewhere on the board
unnamed: C2.1, D1.2 (A), R20.2, R21.2, TP10.1, U2.6 (-)
unnamed: D1.1 (K), R45.2
unnamed: D2.1 (K), F1.2
unnamed: D3.2 (A), R27.2
unnamed: D4.2 (A), R42.2
unnamed: F1.1, FB1.2
unnamed: Q1.1 (C), Q2.1 (C), Q3.1 (C), Q8.1 (C), Q9.1 (C), R11.2, R12.1
unnamed 14: Q4.1 (C), output_BSPD1.2; also elsewhere on the board
unnamed: Q4.2 (B), R43.2
unnamed: Q5.1 (C), Q7.1 (C), R8.1, R22.1, R45.1
unnamed: Q5.2 (B), R6.1
unnamed: Q6.1 (C), R13.1, R42.1, TP14.1
unnamed: Q6.2 (B), R12.2
unnamed: Q7.2 (B), R7.1
unnamed: R1.1, R2.2
unnamed: R2.1, R3.2, R4.2, TP2.1, U2.3 (+)
unnamed: R6.2, TP8.1, U2.1
unnamed: R10.1, R14.2, R19.2
unnamed: R13.2, R43.1
unnamed: R14.1, R19.1, R23.2, R25.2, U6.2 (-)
unnamed: R15.1, SW1.1 (A)
unnamed: R5.2, R16.1, SW1.3 (C)
unnamed: R16.2, R17.1
unnamed: R17.2, R18.1
unnamed: R20.1, R21.1, R22.2
unnamed: R24.1, RV1.1
unnamed: R26.1, U4.1
unnamed: R27.1, R28.1, TP11.1, U2.7
unnamed: R33.1, RV2.1
unnamed: R34.1, U4.7
unnamed: R36.1, R37.2, U3.2 (-)
unnamed: R36.2, U3.6 (-), U3.7
unnamed: R38.1, R39.2, U3.3 (+)
unnamed: R40.1, U5.1
unnamed: R41.1, U5.7
unnamed: RV1.2, U2.5 (+)
unnamed: RV2.2, U3.5 (+)
unnamed: SW1.2 (B), U2.2 (-)
Sinal: R15.2, R37.1, TP6.1, U3.1
current_comp1: Q2.2 (B), R40.2, TP12.1
current_comp2: Q3.2 (B), R41.2, TP13.1
freio_comp3: Q8.2 (B), R26.2
freio_comp4: Q9.2 (B), R34.2
freio_press: R7.2, TP9.1, U6.1
out_bspd: Q1.2 (B), R28.2
sensor_corrente: J1.2, R32.1, R38.2, TP5.1, U5.3 (+), U5.5 (+)
sensor_freio: R9.1, U4.3 (+), U4.5 (+), U6.3 (+), sensor_freio1.2; also elsewhere on the board

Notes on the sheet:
VOLTAGE REFERENCE
Offset and protection for open or short circuit current
BSPD circuit
Vout = (10k/10k) [(V+)-(V-)]
Simula 5.5kW nas baterias
V = 528mV
2.5V - 3.125V
Sinal de corrente 0V - 0.625V
1V - 5V
Open or short circuit current - brake

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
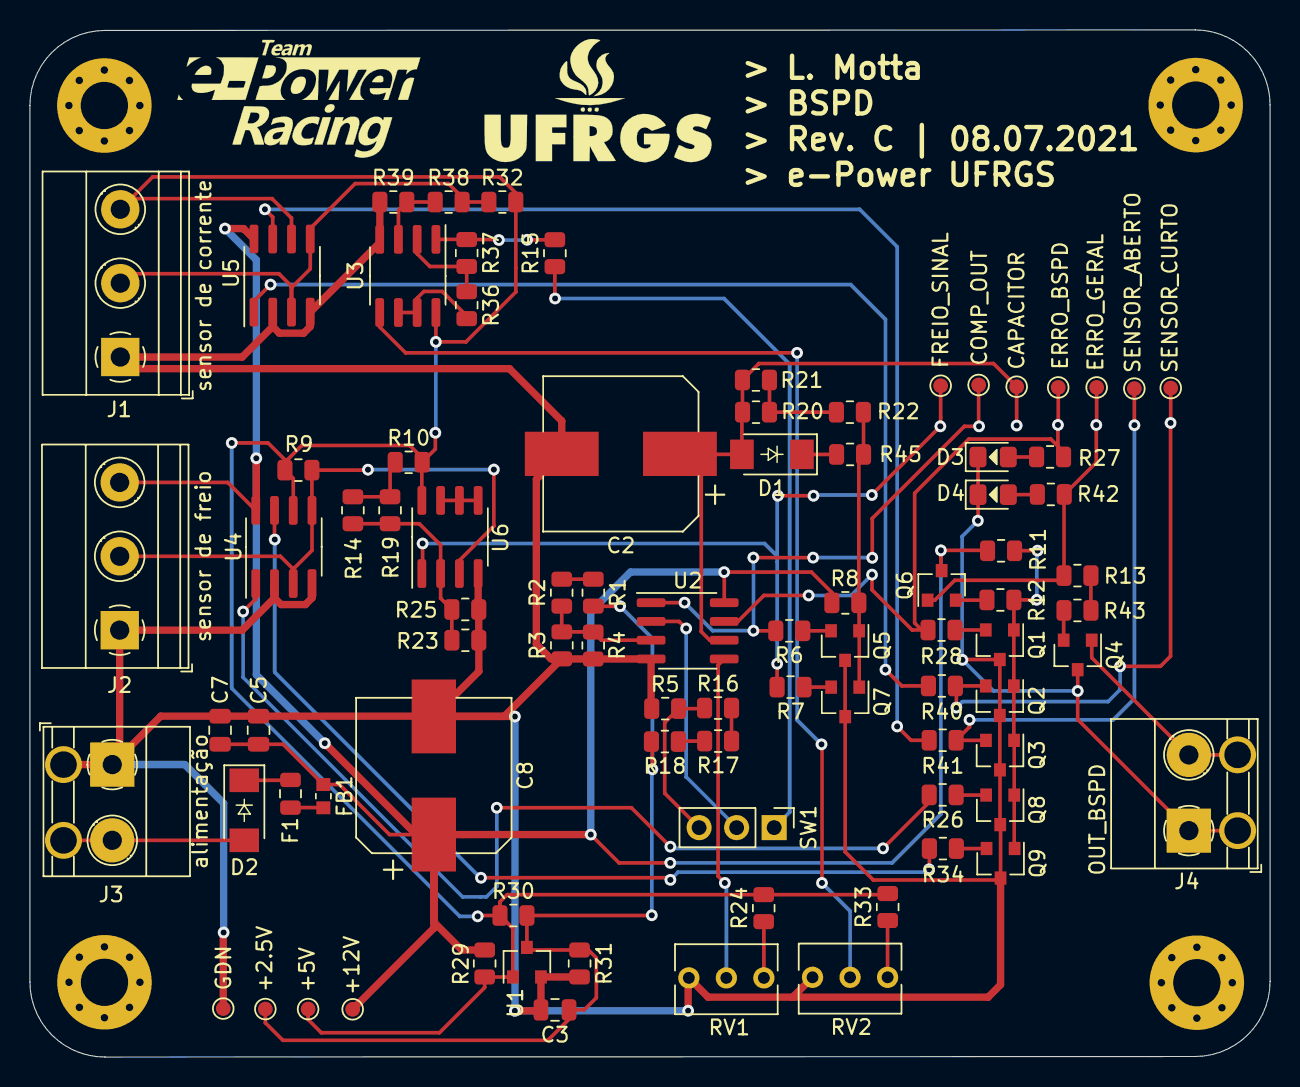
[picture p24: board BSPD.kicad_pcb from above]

Board: 2 copper layers, 84.0 x 69.5 mm, 93 parts (0 on the bottom side), 52 nets.

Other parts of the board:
J2: sensor de freio; TerminalBlock_Phoenix_MKDS-1,5-3_1x03_P5.00mm_Horizontal
J3: alimentação; TerminalBlock_Phoenix_MKDS-1,5-2_1x02_P5.08mm_Horizontal
J4: OUT_BSPD; TerminalBlock_Phoenix_MKDS-1,5-2_1x02_P5.08mm_Horizontal

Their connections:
+12V: J2.3; also elsewhere on the board
Input_Power: J3.2; also elsewhere on the board
unnamed 14: J4.2; also elsewhere on the board
sensor_freio: J2.2; also elsewhere on the board

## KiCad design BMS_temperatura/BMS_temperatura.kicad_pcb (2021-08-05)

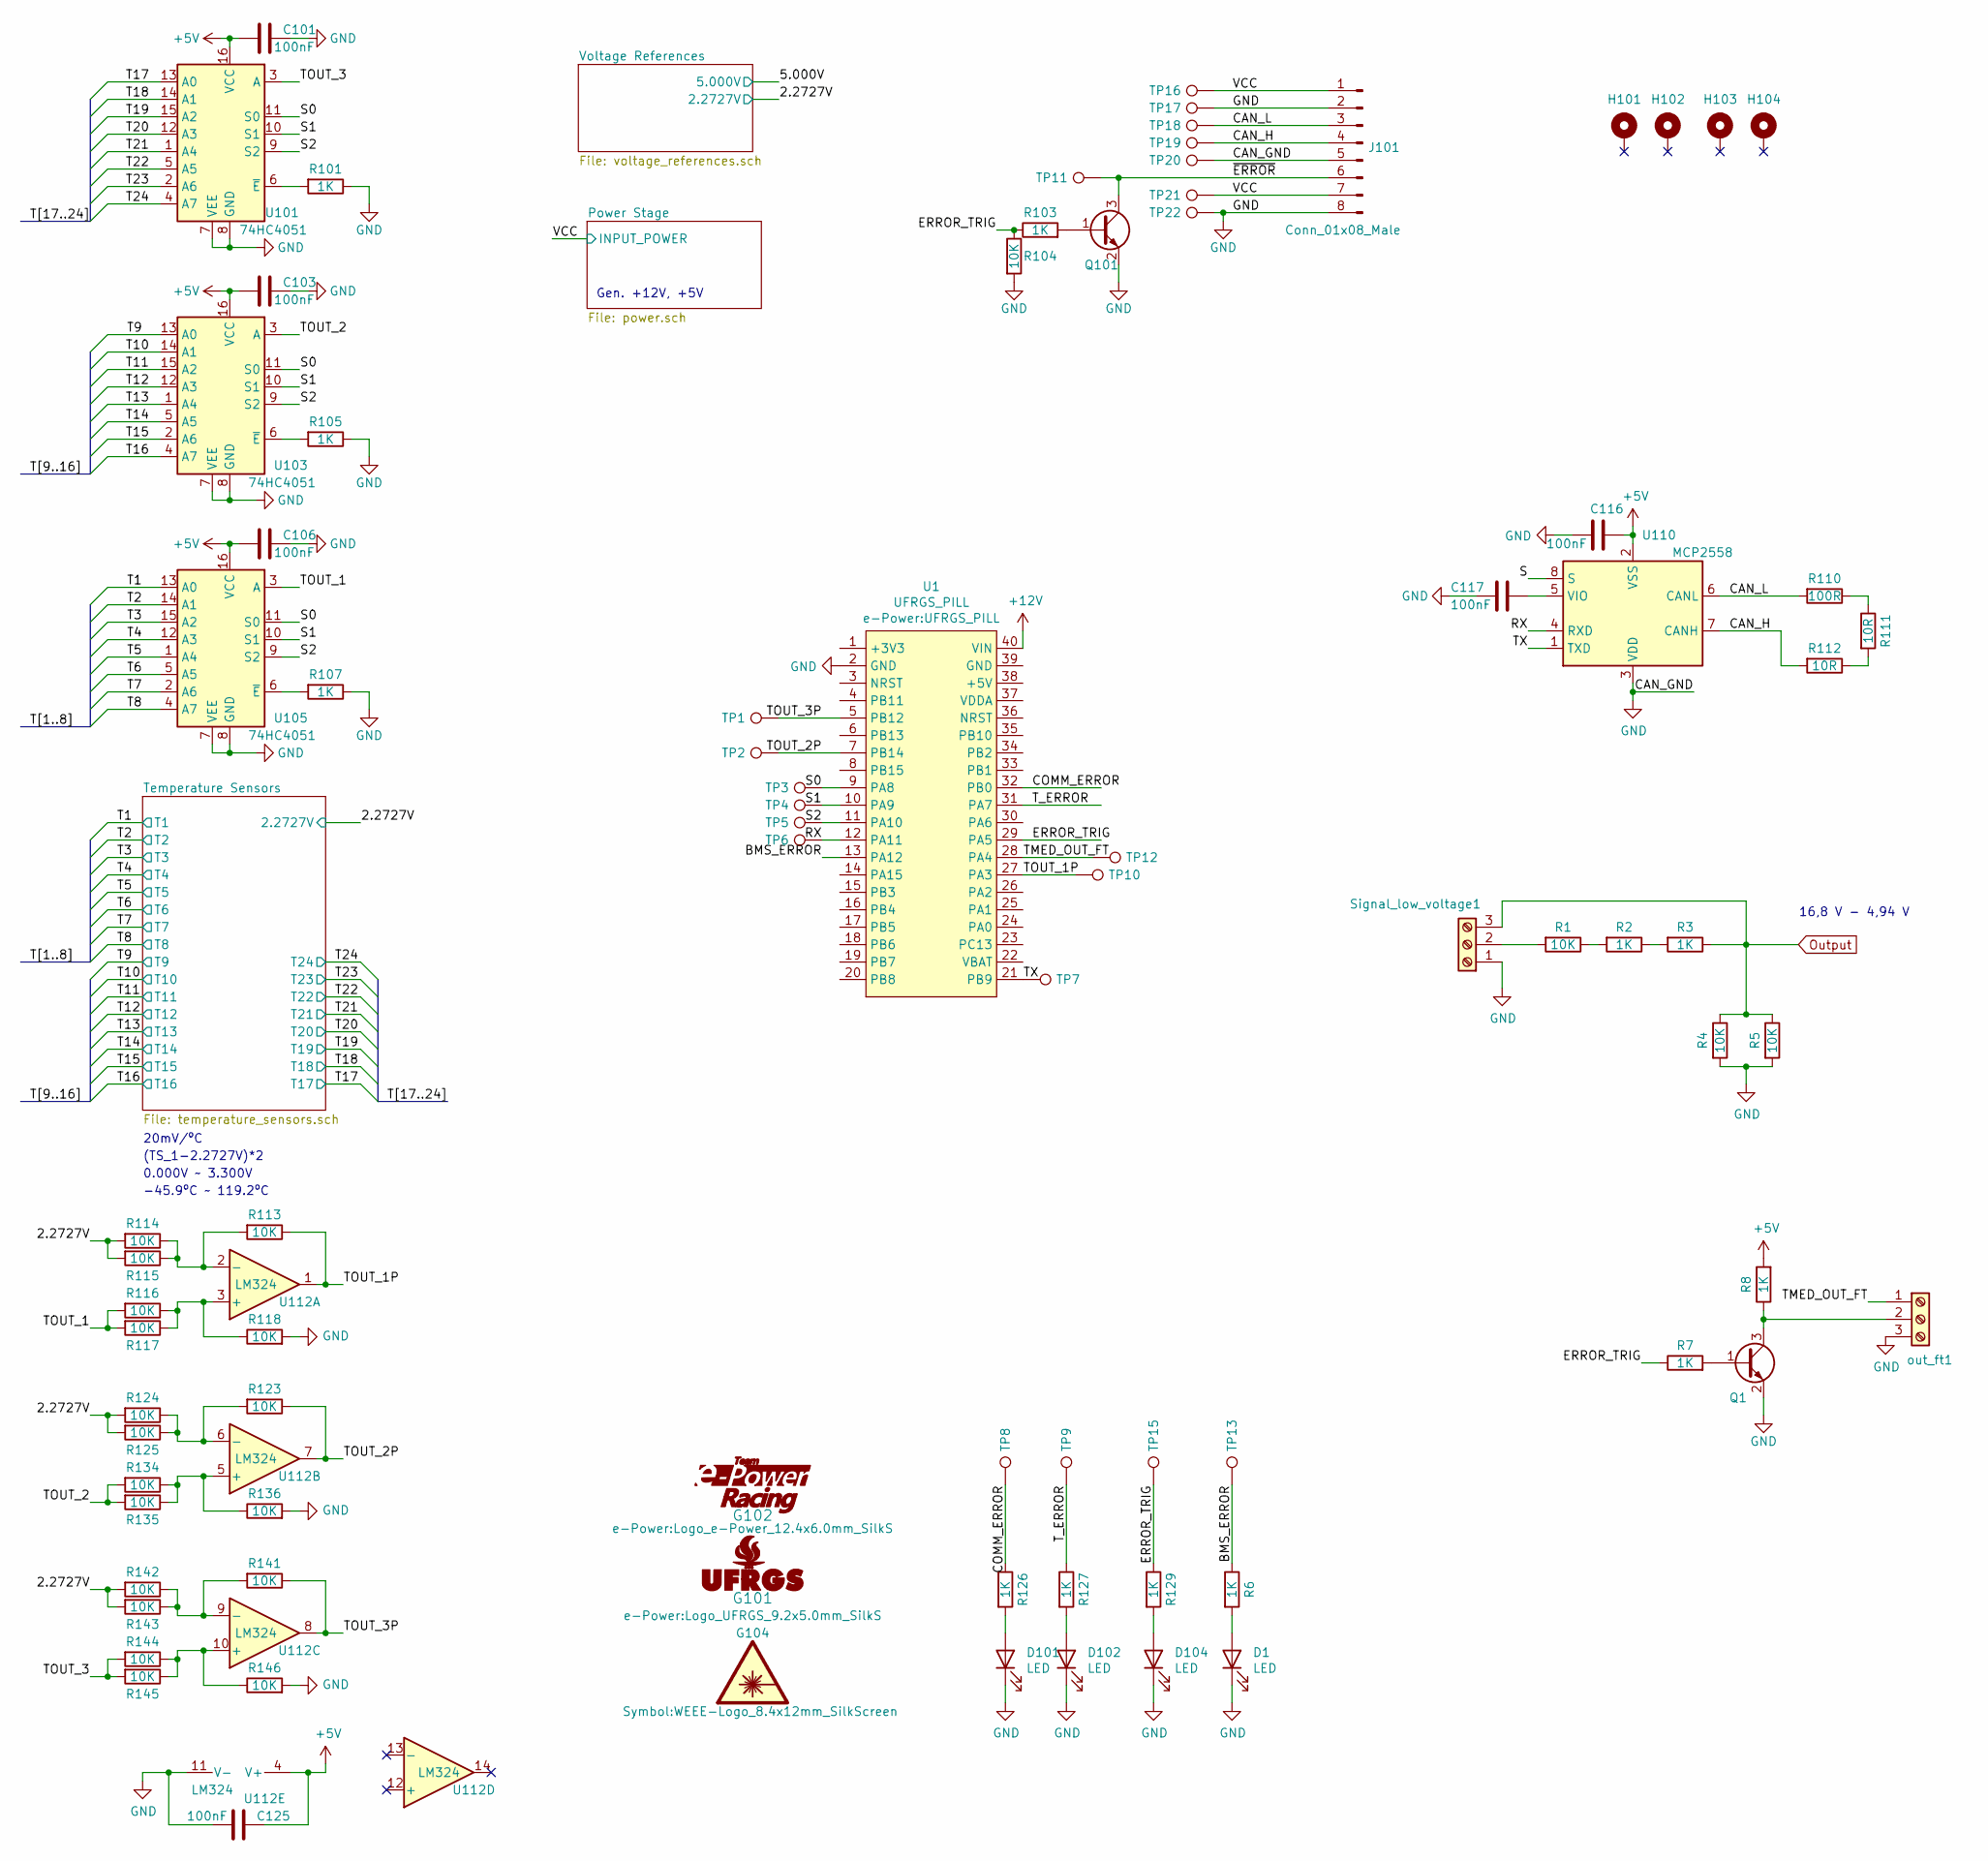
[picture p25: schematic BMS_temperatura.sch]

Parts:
C101, C103, C106, C116, C117, C125: 100nF; C_0805_2012Metric; Voltage 50V; LCSC C49678
D1, D101, D102, D104: LED; LED_0805_1.15x1.40mm_HandSolder
G101: Logo_UFRGS_Large; Logo_UFRGS_9.2x5.0mm_SilkS
G102: Logo_e-Power_Large; Logo_e-Power_12.4x6.0mm_SilkS
G104: SYM_LASER_Large; WEEE-Logo_8.4x12mm_SilkScreen
H101, H102, H103, H104: GND; MountingHole_3.2mm_M3_Pad_Via
J101: Conn_01x08_Male; Molex_Mini-Fit_Jr_2x04_P4.20mm_Horizontal
Q1, Q101: MMBT3904; SOT-23; LCSC C20526
R1, R4, R5: 10K; R_0805_2012Metric; Voltage 150V; LCSC C17513
R2, R3, R6, R7, R8, R101, R103, R105, R107, R126, R127, R129: 1K; R_0805_2012Metric; Voltage 150V; LCSC C17513
R104, R113, R114, R115, R116, R117, R118, R123, R124, R125, R134, R135, R136, R141, R142, R143, R144, R145, R146: 10K; R_0805_2012Metric; Voltage 150V; LCSC C17414
R110: 100R; R_0805_2012Metric; Voltage 150V; LCSC C17408
R111, R112: 10R; R_0805_2012Metric; Voltage 150V; LCSC C17415
Signal_low_voltage1: Screw_Terminal_01x03; TerminalBlock_Phoenix_MKDS-1,5-3_1x03_P5.00mm_Horizontal
TP1: TOUT_3P; TestPoint_Pad_D1.0mm
TP2: TOUT_2P; TestPoint_Pad_D1.0mm
TP3: S0; TestPoint_Pad_D1.0mm
TP4: S1; TestPoint_Pad_D1.0mm
TP5: S2; TestPoint_Pad_D1.0mm
TP6: RX; TestPoint_Pad_D1.0mm
TP7: TX; TestPoint_Pad_D1.0mm
TP8: C_ERROR; TestPoint_Pad_D1.0mm
TP9: T_ERROR; TestPoint_Pad_D1.0mm
TP10: TOUT_1P; TestPoint_Pad_D1.0mm
TP11: ~ERROR; TestPoint_Pad_D1.0mm
TP12: TMED_OUT_FT; TestPoint_Pad_D1.0mm
TP13: BMS_ERROR; TestPoint_Pad_D1.0mm
TP15: ERROR_TRIG; TestPoint_Pad_D1.0mm
TP16, TP21: VCC; TestPoint_Pad_D1.0mm
TP17: GND; TestPoint_Pad_D1.0mm
TP18: CAN_L; TestPoint_Pad_D1.0mm
TP19: CAN_H; TestPoint_Pad_D1.0mm
TP20: CAN_GND; TestPoint_Pad_D1.0mm
TP22: GNG; TestPoint_Pad_D1.0mm
U1: UFRGS_PILL
U101, U103, U105: 74HC4051; SOP-16_4.4x10.4mm_P1.27mm; LCSC C9386
U110: MCP2558; SOIC-8_3.9x4.9mm_P1.27mm
U112: LM324; SOIC-14_3.9x8.7mm_P1.27mm; LCSC C71035
out_ft1: Screw_Terminal_01x03; TerminalBlock_Phoenix_MKDS-1,5-3_1x03_P5.00mm_Horizontal

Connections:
+5V: C101.2, C103.2, C106.2, C116.1, C125.1, R8.2, U101.16 (VCC), U103.16 (VCC), U105.16 (VCC), U110.2 (VSS), U112.4 (V+); also elsewhere on the board
+12V: U1.40 (VIN); also elsewhere on the board
/2.2727V: R114.2, R115.2, R124.2, R125.2, R142.2, R143.2; also elsewhere on the board
/BMS_ERROR: R6.1, TP13.1, U1.13 (PA12)
/CAN_H: J101.4, R112.2, TP19.1, U110.7 (CANH)
/CAN_L: J101.3, R110.2, TP18.1, U110.6 (CANL)
/COMM_ERROR: R126.1, TP8.1, U1.32 (PB0)
/ERROR_TRIG: R7.1, R103.1, R104.1, R129.1, TP15.1, U1.29 (PA5)
/RX: TP6.1, U1.12 (PA11), U110.4 (RXD)
/S: U110.8 (S)
/S0: TP3.1, U1.9 (PA8), U101.11 (S0), U103.11 (S0), U105.11 (S0)
/S1: TP4.1, U1.10 (PA9), U101.10 (S1), U103.10 (S1), U105.10 (S1)
/S2: TP5.1, U1.11 (PA10), U101.9 (S2), U103.9 (S2), U105.9 (S2)
/T1: U105.13 (A0); also elsewhere on the board
/T2: U105.14 (A1); also elsewhere on the board
/T3: U105.15 (A2); also elsewhere on the board
/T4: U105.12 (A3); also elsewhere on the board
/T5: U105.1 (A4); also elsewhere on the board
/T6: U105.5 (A5); also elsewhere on the board
/T7: U105.2 (A6); also elsewhere on the board
/T8: U105.4 (A7); also elsewhere on the board
/T9: U103.13 (A0); also elsewhere on the board
/T10: U103.14 (A1); also elsewhere on the board
/T11: U103.15 (A2); also elsewhere on the board
/T12: U103.12 (A3); also elsewhere on the board
/T13: U103.1 (A4); also elsewhere on the board
/T14: U103.5 (A5); also elsewhere on the board
/T15: U103.2 (A6); also elsewhere on the board
/T16: U103.4 (A7); also elsewhere on the board
/T17: U101.13 (A0); also elsewhere on the board
/T18: U101.14 (A1); also elsewhere on the board
/T19: U101.15 (A2); also elsewhere on the board
/T20: U101.12 (A3); also elsewhere on the board
/T21: U101.1 (A4); also elsewhere on the board
/T22: U101.5 (A5); also elsewhere on the board
/T23: U101.2 (A6); also elsewhere on the board
/T24: U101.4 (A7); also elsewhere on the board
/TMED_OUT_FT: TP12.1, U1.28 (PA4), out_ft1.1
/TOUT_1: R116.2, R117.2, U105.3 (A)
/TOUT_1P: R113.1, TP10.1, U1.27 (PA3), U112.1
/TOUT_2: R134.2, R135.2, U103.3 (A)
/TOUT_2P: R123.1, TP2.1, U1.7 (PB14), U112.7
/TOUT_3: R144.2, R145.2, U101.3 (A)
/TOUT_3P: R141.1, TP1.1, U1.5 (PB12), U112.8
/TX: TP7.1, U1.21 (PB9), U110.1 (TXD)
/T_ERROR: R127.1, TP9.1, U1.31 (PA7)
/VCC: J101.1, J101.7, TP16.1, TP21.1; also elsewhere on the board
/~ERROR: J101.6, Q101.3 (C), TP11.1
GND: C101.1, C103.1, C106.1, C116.2, C117.2, C125.2, D1.1 (K), D101.1 (K), D102.1 (K), D104.1 (K), J101.2, J101.5, J101.8, Q1.2 (E), Q101.2 (E), R4.2, R5.2, R101.1, R104.2, R105.1, R107.1, R118.2, R136.2, R146.2, Signal_low_voltage1.1, TP17.1, TP20.1, TP22.1, U1.2 (GND), U101.7 (VEE), U101.8 (GND), U103.7 (VEE), U103.8 (GND), U105.7 (VEE), U105.8 (GND), U110.3 (VDD), U112.11 (V-), out_ft1.3; also elsewhere on the board
unnamed: C117.1, U110.5 (VIO)
unnamed: D1.2 (A), R6.2
unnamed: D101.2 (A), R126.2
unnamed: D102.2 (A), R127.2
unnamed: D104.2 (A), R129.2
unnamed: Q1.1 (B), R7.2
unnamed: Q1.3 (C), R8.1, out_ft1.2
unnamed: Q101.1 (B), R103.2
unnamed: R1.1, R2.2
unnamed: R1.2, Signal_low_voltage1.2
unnamed: R2.1, R3.2
unnamed: R101.2, U101.6 (~E)
unnamed: R105.2, U103.6 (~E)
unnamed: R107.2, U105.6 (~E)
unnamed: R110.1, R111.1
unnamed: R111.2, R112.1
unnamed: R113.2, R114.1, R115.1, U112.2 (-)
unnamed: R116.1, R117.1, R118.1, U112.3 (+)
unnamed: R123.2, R124.1, R125.1, U112.6 (-)
unnamed: R134.1, R135.1, R136.1, U112.5 (+)
unnamed: R141.2, R142.1, R143.1, U112.9 (-)
unnamed: R144.1, R145.1, R146.1, U112.10 (+)
Output: R3.1, R4.1, R5.1, Signal_low_voltage1.3

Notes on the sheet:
Gen. +12V, +5V
-45.9ºC ~~ 119.2ºC
0.000V ~~ 3.300V
(TS_1-2.2727V)*2
20mV/ºC
16,8 V - 4,94 V

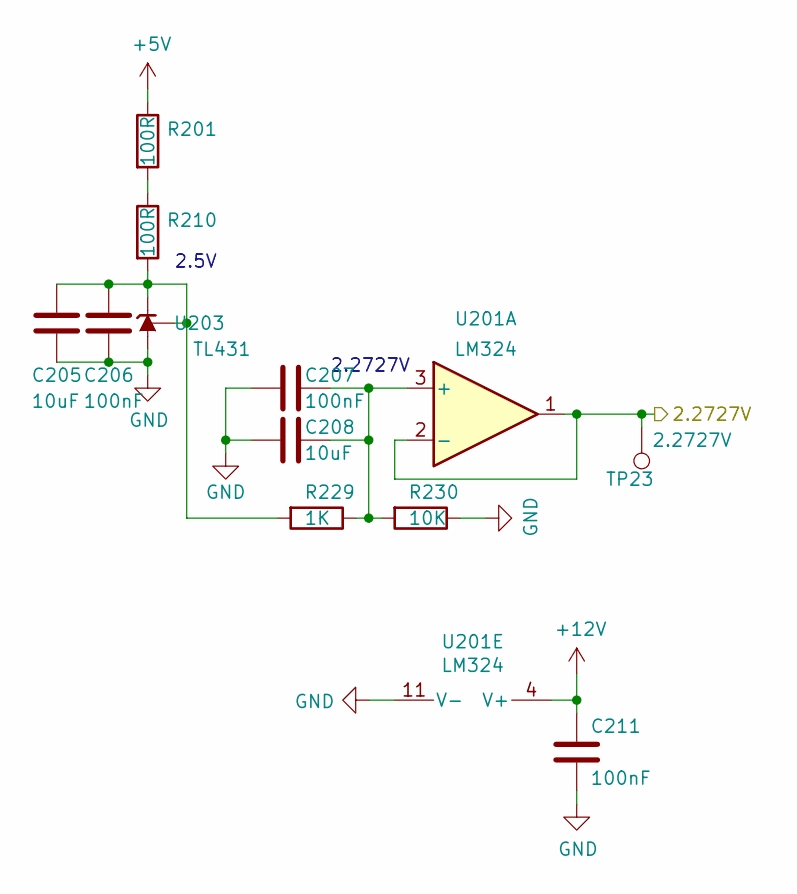
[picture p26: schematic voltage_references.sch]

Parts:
C205, C208: 10uF; C_0805_2012Metric; LCSC C15850
C206, C207, C211: 100nF; C_0805_2012Metric; Voltage 50V; LCSC C49678
R201, R210: 100R; R_0805_2012Metric; LCSC C17408
R229: 1K; R_0805_2012Metric; Voltage 150V; LCSC C17513
R230: 10K; R_0805_2012Metric; Voltage 150V; LCSC C17414
TP23: 2.2727V; TestPoint_Pad_D1.0mm
U201: LM324; SOIC-14_3.9x8.7mm_P1.27mm; LCSC C71035
U203: TL431; SOT-23; LCSC C3113

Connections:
+5V: R201.1; also elsewhere on the board
+12V: C211.1, U201.4 (V+); also elsewhere on the board
/2.2727V: TP23.1, U201.1, U201.2 (-); also elsewhere on the board
GND: C205.2, C206.2, C207.2, C208.2, C211.2, R230.1, U201.11 (V-), U203.3 (A); also elsewhere on the board
unnamed: C205.1, C206.1, R210.2, R229.2, U203.1 (REF), U203.2 (K)
unnamed: C207.1, C208.1, R229.1, R230.2, U201.3 (+)
unnamed: R201.2, R210.1

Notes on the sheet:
2.5V
2.2727V

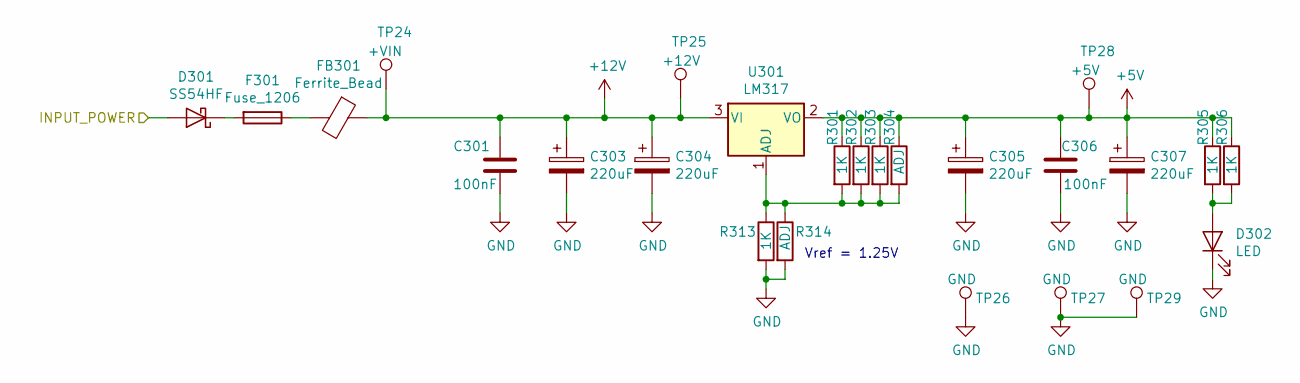
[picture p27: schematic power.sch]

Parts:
C301, C306: 100nF; C_0805_2012Metric; Voltage 50V; LCSC C49678
C303, C304, C305, C307: 220uF; CP_Elec_10x10
D301: SS54HF; DO-214AC
D302: LED; LED_0805_1.15x1.40mm_HandSolder
F301: Fuse_1206; FUSE_1206_3216Metric
FB301: Ferrite_Bead; FB_0805_2012Metric; LCSC C1017
R301, R302, R303, R305, R306, R313: 1K; R_0805_2012Metric; Voltage 150V; LCSC C17513
R304, R314: ADJ; R_0805_2012Metric
TP24: +VIN; TestPoint_Pad_D1.0mm
TP25: +12V; TestPoint_Pad_D1.0mm
TP26, TP27, TP29: GND; TestPoint_Pad_D1.0mm
TP28: +5V; TestPoint_Pad_D1.0mm
U301: LM317; TO-220-3_Horizontal_TabDown

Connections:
+5V: C305.1, C306.1, C307.1, R301.1, R302.1, R303.1, R304.1, R305.1, R306.1, TP28.1, U301.2 (VO); also elsewhere on the board
+12V: C301.1, C303.1, C304.1, FB301.1, TP24.1, TP25.1, U301.3 (VI); also elsewhere on the board
/VCC: D301.2 (A); also elsewhere on the board
GND: C301.2, C303.2, C304.2, C305.2, C306.2, C307.2, D302.1 (K), R313.2, R314.2, TP26.1, TP27.1, TP29.1; also elsewhere on the board
unnamed: D301.1 (K), F301.2
unnamed: D302.2 (A), R305.2, R306.2
unnamed: F301.1, FB301.2
unnamed: R301.2, R302.2, R303.2, R304.2, R313.1, R314.1, U301.1 (ADJ)

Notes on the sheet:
Vref = 1.25V

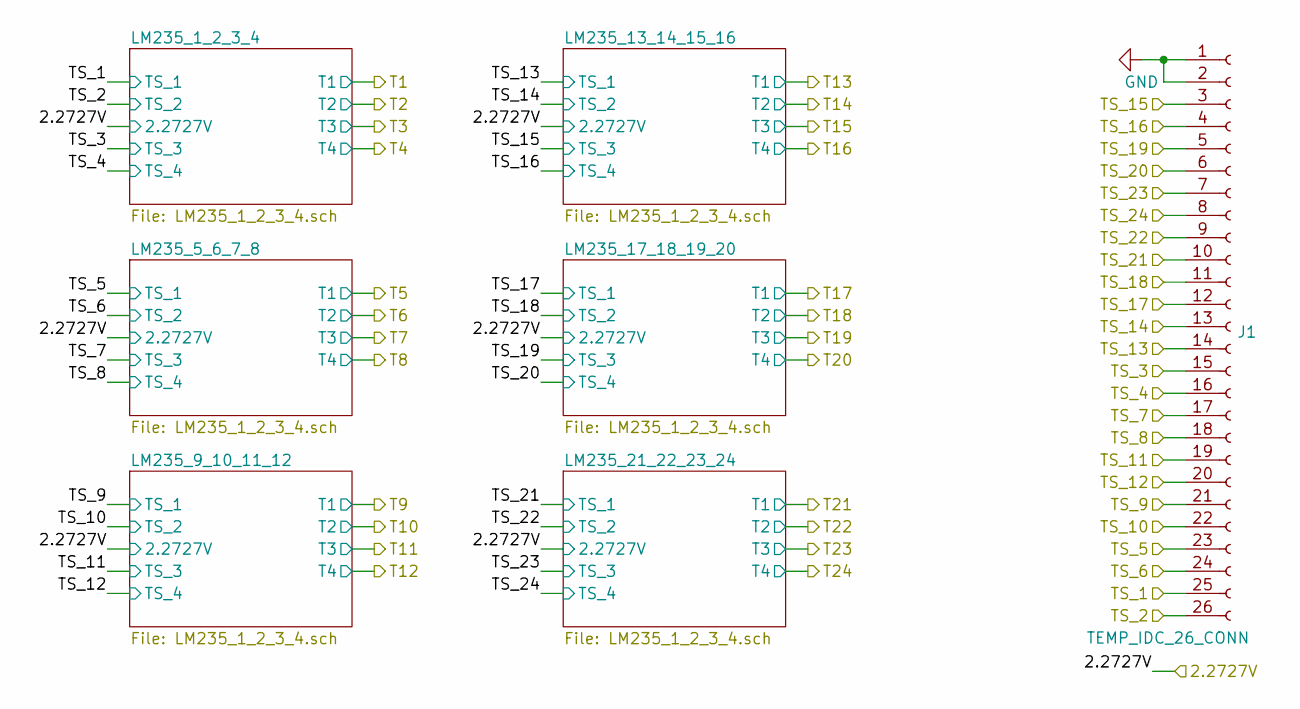
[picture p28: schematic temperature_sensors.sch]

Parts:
J1: TEMP_IDC_26_CONN; IDC-Header_2x13_P2.54mm_Horizontal

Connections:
/Temperature Sensors/TS_1: J1.25; also elsewhere on the board
/Temperature Sensors/TS_2: J1.26; also elsewhere on the board
/Temperature Sensors/TS_3: J1.15; also elsewhere on the board
/Temperature Sensors/TS_4: J1.16; also elsewhere on the board
/Temperature Sensors/TS_5: J1.23; also elsewhere on the board
/Temperature Sensors/TS_6: J1.24; also elsewhere on the board
/Temperature Sensors/TS_7: J1.17; also elsewhere on the board
/Temperature Sensors/TS_8: J1.18; also elsewhere on the board
/Temperature Sensors/TS_9: J1.21; also elsewhere on the board
/Temperature Sensors/TS_10: J1.22; also elsewhere on the board
/Temperature Sensors/TS_11: J1.19; also elsewhere on the board
/Temperature Sensors/TS_12: J1.20; also elsewhere on the board
/Temperature Sensors/TS_13: J1.14; also elsewhere on the board
/Temperature Sensors/TS_14: J1.13; also elsewhere on the board
/Temperature Sensors/TS_15: J1.3; also elsewhere on the board
/Temperature Sensors/TS_16: J1.4; also elsewhere on the board
/Temperature Sensors/TS_17: J1.12; also elsewhere on the board
/Temperature Sensors/TS_18: J1.11; also elsewhere on the board
/Temperature Sensors/TS_19: J1.5; also elsewhere on the board
/Temperature Sensors/TS_20: J1.6; also elsewhere on the board
/Temperature Sensors/TS_21: J1.10; also elsewhere on the board
/Temperature Sensors/TS_22: J1.9; also elsewhere on the board
/Temperature Sensors/TS_23: J1.7; also elsewhere on the board
/Temperature Sensors/TS_24: J1.8; also elsewhere on the board
GND: J1.1, J1.2; also elsewhere on the board

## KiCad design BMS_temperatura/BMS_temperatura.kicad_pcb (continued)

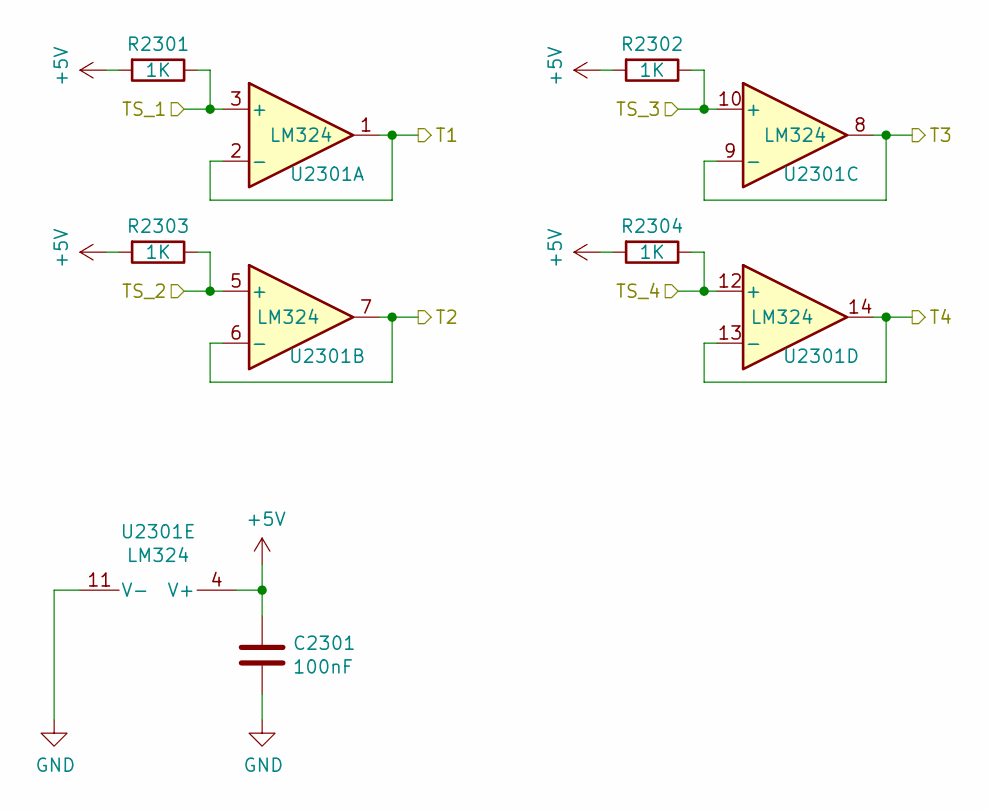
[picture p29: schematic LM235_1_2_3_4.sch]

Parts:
C2001: 100nF; C_0805_2012Metric; Voltage 50V; LCSC C49678
R2001, R2002, R2003, R2004: 1K; R_0805_2012Metric; Voltage 150V; LCSC C17513
U2001: LM324; SOIC-14_3.9x8.7mm_P1.27mm; LCSC C71035

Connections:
+5V: C2001.1, R2001.2, R2002.2, R2003.2, R2004.2, U2001.4 (V+); also elsewhere on the board
/T1: U2001.1, U2001.2 (-); also elsewhere on the board
/T2: U2001.6 (-), U2001.7; also elsewhere on the board
/T3: U2001.8, U2001.9 (-); also elsewhere on the board
/T4: U2001.13 (-), U2001.14; also elsewhere on the board
/Temperature Sensors/TS_1: R2001.1, U2001.3 (+); also elsewhere on the board
/Temperature Sensors/TS_2: R2003.1, U2001.5 (+); also elsewhere on the board
/Temperature Sensors/TS_3: R2002.1, U2001.10 (+); also elsewhere on the board
/Temperature Sensors/TS_4: R2004.1, U2001.12 (+); also elsewhere on the board
GND: C2001.2, U2001.11 (V-); also elsewhere on the board

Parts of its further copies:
C1801, C1901, C2101, C2201, C2301: 100nF; C_0805_2012Metric; Voltage 50V; LCSC C49678
R1801, R1802, R1803, R1804, R1901, R1902, R1903, R1904, R2101, R2102, R2103, R2104, R2201, R2202, R2203, R2204, R2301, R2302, R2303, R2304: 1K; R_0805_2012Metric; Voltage 150V; LCSC C17513
U1801, U1901, U2101, U2201, U2301: LM324; SOIC-14_3.9x8.7mm_P1.27mm; LCSC C71035

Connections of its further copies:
+5V: C1801.1, C1901.1, C2101.1, C2201.1, C2301.1, R1801.2, R1802.2, R1803.2, R1804.2, R1901.2, R1902.2, R1903.2, R1904.2, R2101.2, R2102.2, R2103.2, R2104.2, R2201.2, R2202.2, R2203.2, R2204.2, R2301.2, R2302.2, R2303.2, R2304.2, U1801.4 (V+), U1901.4 (V+), U2101.4 (V+), U2201.4 (V+), U2301.4 (V+); also elsewhere on the board
/T5: U1801.1, U1801.2 (-); also elsewhere on the board
/T6: U1801.6 (-), U1801.7; also elsewhere on the board
/T7: U1801.8, U1801.9 (-); also elsewhere on the board
/T8: U1801.13 (-), U1801.14; also elsewhere on the board
/T9: U1901.1, U1901.2 (-); also elsewhere on the board
/T10: U1901.6 (-), U1901.7; also elsewhere on the board
/T11: U1901.8, U1901.9 (-); also elsewhere on the board
/T12: U1901.13 (-), U1901.14; also elsewhere on the board
/T13: U2101.1, U2101.2 (-); also elsewhere on the board
/T14: U2101.6 (-), U2101.7; also elsewhere on the board
/T15: U2101.8, U2101.9 (-); also elsewhere on the board
/T16: U2101.13 (-), U2101.14; also elsewhere on the board
/T17: U2201.1, U2201.2 (-); also elsewhere on the board
/T18: U2201.6 (-), U2201.7; also elsewhere on the board
/T19: U2201.8, U2201.9 (-); also elsewhere on the board
/T20: U2201.13 (-), U2201.14; also elsewhere on the board
/T21: U2301.1, U2301.2 (-); also elsewhere on the board
/T22: U2301.6 (-), U2301.7; also elsewhere on the board
/T23: U2301.8, U2301.9 (-); also elsewhere on the board
/T24: U2301.13 (-), U2301.14; also elsewhere on the board
/Temperature Sensors/TS_5: R1801.1, U1801.3 (+); also elsewhere on the board
/Temperature Sensors/TS_6: R1803.1, U1801.5 (+); also elsewhere on the board
/Temperature Sensors/TS_7: R1802.1, U1801.10 (+); also elsewhere on the board
/Temperature Sensors/TS_8: R1804.1, U1801.12 (+); also elsewhere on the board
/Temperature Sensors/TS_9: R1901.1, U1901.3 (+); also elsewhere on the board
/Temperature Sensors/TS_10: R1903.1, U1901.5 (+); also elsewhere on the board
/Temperature Sensors/TS_11: R1902.1, U1901.10 (+); also elsewhere on the board
/Temperature Sensors/TS_12: R1904.1, U1901.12 (+); also elsewhere on the board
/Temperature Sensors/TS_13: R2101.1, U2101.3 (+); also elsewhere on the board
/Temperature Sensors/TS_14: R2103.1, U2101.5 (+); also elsewhere on the board
/Temperature Sensors/TS_15: R2102.1, U2101.10 (+); also elsewhere on the board
/Temperature Sensors/TS_16: R2104.1, U2101.12 (+); also elsewhere on the board
/Temperature Sensors/TS_17: R2201.1, U2201.3 (+); also elsewhere on the board
/Temperature Sensors/TS_18: R2203.1, U2201.5 (+); also elsewhere on the board
/Temperature Sensors/TS_19: R2202.1, U2201.10 (+); also elsewhere on the board
/Temperature Sensors/TS_20: R2204.1, U2201.12 (+); also elsewhere on the board
/Temperature Sensors/TS_21: R2301.1, U2301.3 (+); also elsewhere on the board
/Temperature Sensors/TS_22: R2303.1, U2301.5 (+); also elsewhere on the board
/Temperature Sensors/TS_23: R2302.1, U2301.10 (+); also elsewhere on the board
/Temperature Sensors/TS_24: R2304.1, U2301.12 (+); also elsewhere on the board
GND: C1801.2, C1901.2, C2101.2, C2201.2, C2301.2, U1801.11 (V-), U1901.11 (V-), U2101.11 (V-), U2201.11 (V-), U2301.11 (V-); also elsewhere on the board

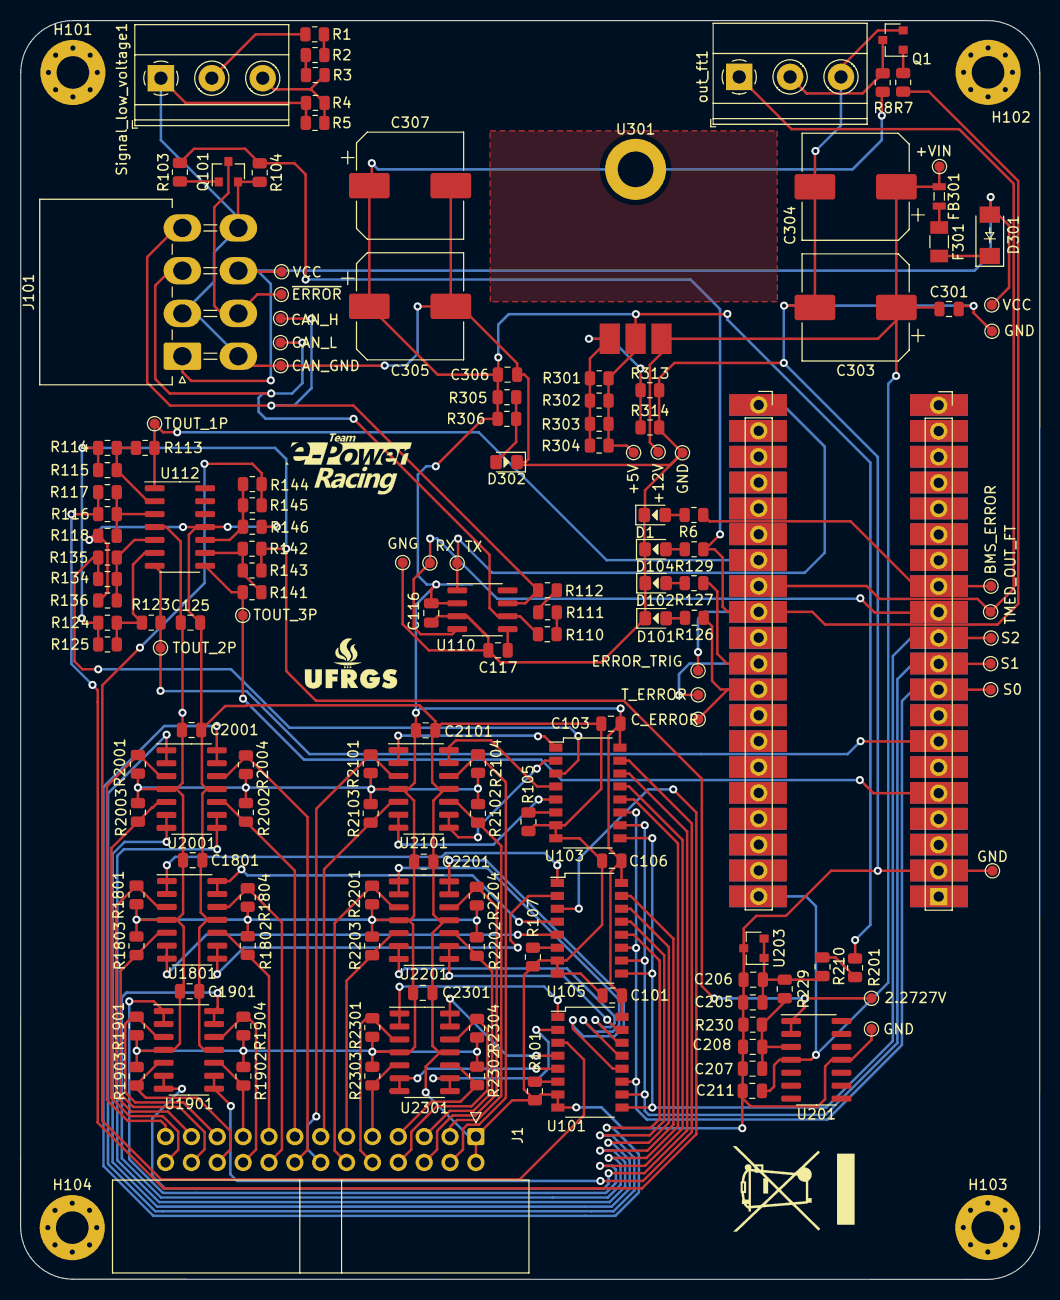
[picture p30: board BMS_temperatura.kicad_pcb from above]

Board: 2 copper layers, 100.1 x 123.6 mm, 160 parts (0 on the bottom side), 102 nets.

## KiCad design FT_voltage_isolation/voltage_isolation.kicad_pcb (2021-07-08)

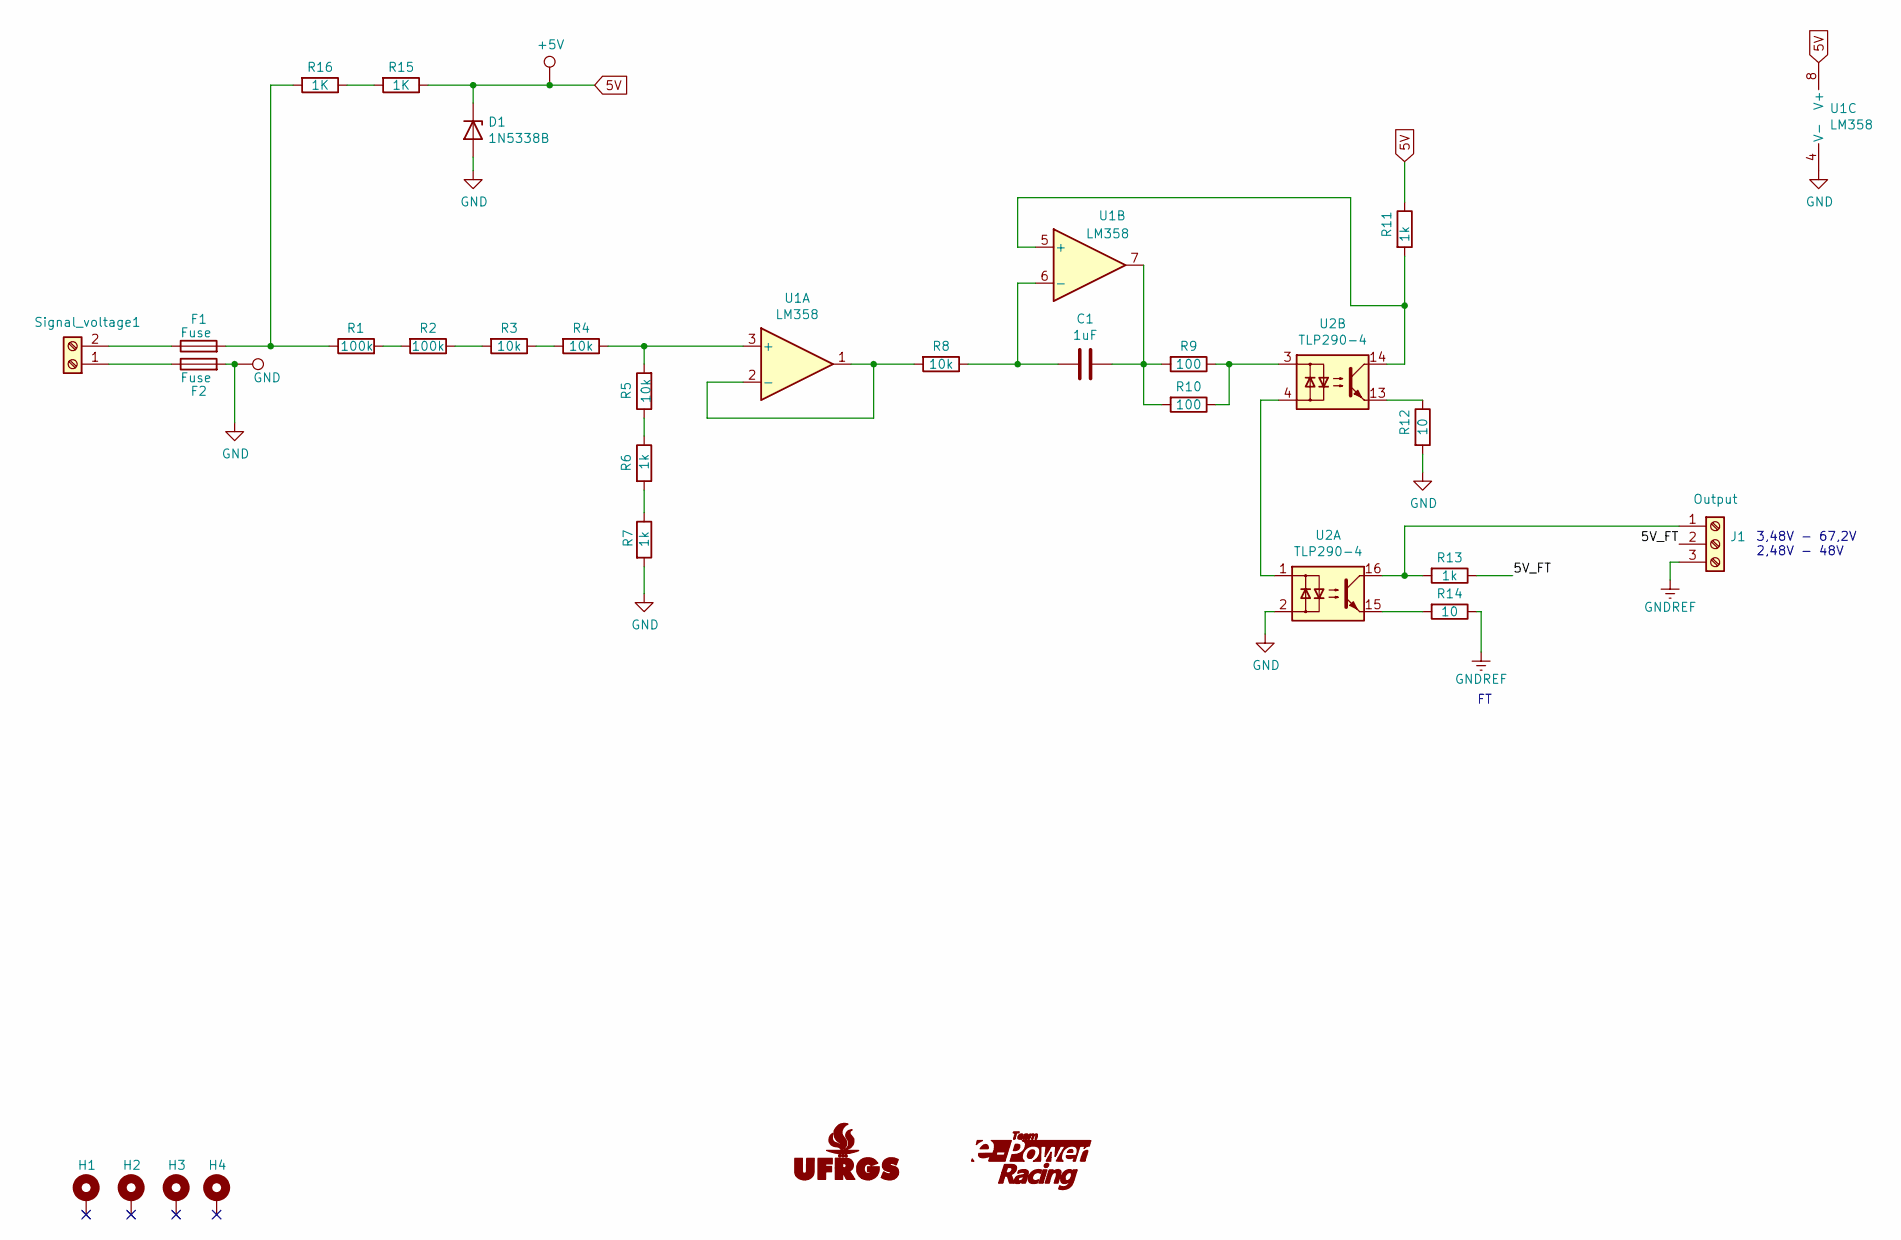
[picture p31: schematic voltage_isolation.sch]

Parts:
C1: 1uF; C_0805_2012Metric
D1: 1N5338B; D_DO-201_P15.24mm_Horizontal
F1, F2: Fuse; FUSE_1206_3216Metric
G1: Logo_UFRGS_Large; Logo_UFRGS_14.7x8.0mm_SilkS
G2: Logo_e-Power_Large; Logo_e-Power_16.5x8.0mm_SilkS
H1, H2, H3, H4: MountingHole_Pad; MountingHole_3.2mm_M3_Pad_Via
J1: Output; TerminalBlock_Phoenix_MKDS-1,5-3_1x03_P5.00mm_Horizontal
R1, R2: 100k; R_0805_2012Metric
R3, R4, R5, R8: 10k; R_0805_2012Metric
R6, R7, R11, R13: 1k; R_0805_2012Metric
R9, R10: 100; R_0805_2012Metric
R12, R14: 10; R_0805_2012Metric
R15, R16: 1K; R_Axial_DIN0207_L6.3mm_D2.5mm_P10.16mm_Horizontal
Signal_voltage1: Screw_Terminal_01x02; TerminalBlock_Phoenix_MKDS-1,5-2_1x02_P5.08mm_Horizontal
TP1: +5V; TestPoint_Pad_D1.0mm
TP2: GND; TestPoint_Pad_D1.0mm
U1: LM358; SOIC-8_3.9x4.9mm_P1.27mm
U2: TLP290-4; SOIC-16_4.55x10.3mm_P1.27mm(TLP290-4)

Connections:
5V: D1.1 (K), R11.1, R15.1, TP1.1, U1.8 (V+)
/5V_FT: J1.2, R13.1
GND: D1.2 (A), F2.2, R7.2, R12.2, TP2.1, U1.4 (V-), U2.2
GNDREF: J1.3, R14.1
unnamed: C1.1, R9.2, R10.2, U1.7
unnamed: C1.2, R8.1, U1.6 (-)
unnamed: F1.1, Signal_voltage1.2
unnamed: F1.2, R1.1, R16.2
unnamed: F2.1, Signal_voltage1.1
unnamed: J1.1, R13.2, U2.16
unnamed: R1.2, R2.2
unnamed: R2.1, R3.2
unnamed: R3.1, R4.2
unnamed: R4.1, R5.2, U1.3 (+)
unnamed: R5.1, R6.1
unnamed: R6.2, R7.1
unnamed: R8.2, U1.1, U1.2 (-)
unnamed: R9.1, R10.1, U2.3
unnamed: R11.2, U1.5 (+), U2.14
unnamed: R12.1, U2.13
unnamed: R14.2, U2.15
unnamed: R15.2, R16.1
unnamed: U2.1, U2.4

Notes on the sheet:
3,48V - 67,2V 2,48V - 48V

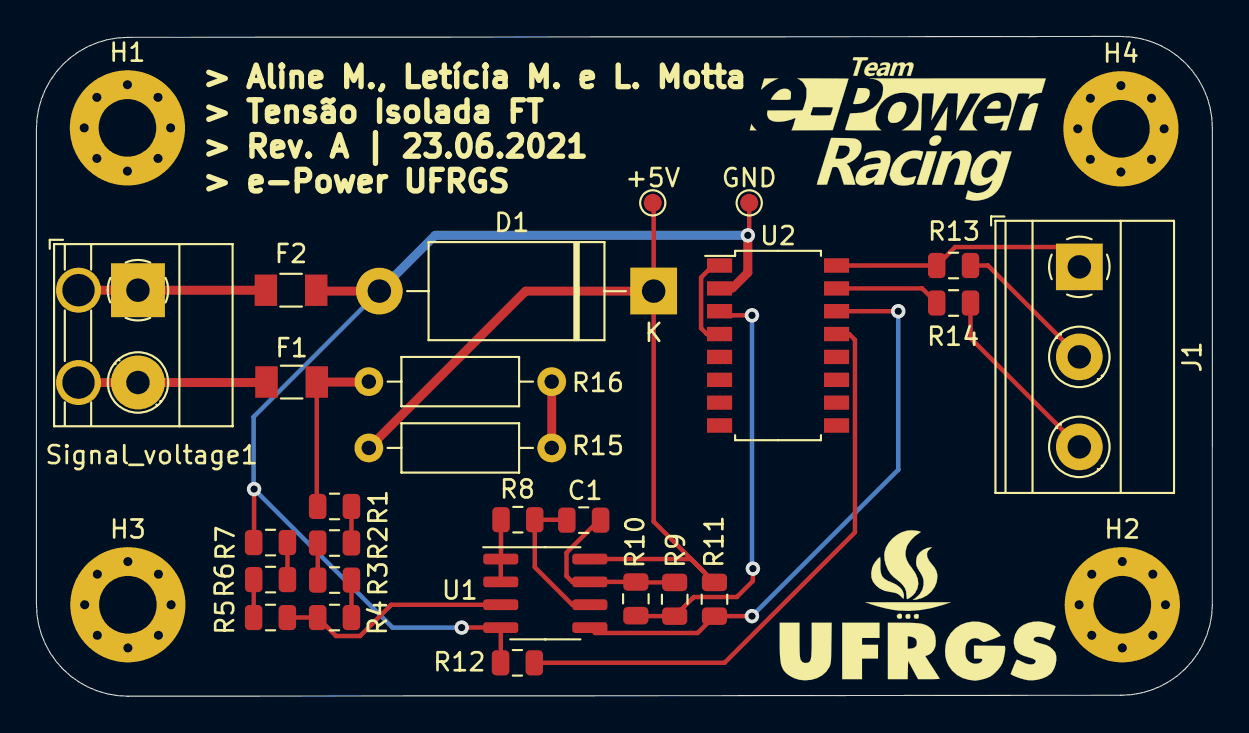
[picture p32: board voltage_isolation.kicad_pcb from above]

Board: 2 copper layers, 65.3 x 36.7 mm, 32 parts (0 on the bottom side), 23 nets.

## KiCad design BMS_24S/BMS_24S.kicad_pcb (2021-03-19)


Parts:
C101, C102, C103, C104, C105, C106, C107, C108, C113, C115, C116, C117, C118, C119, C120, C121, C122, C125, C126: 100nF; C_0805_2012Metric; Voltage 50V; LCSC C49678
C109, C110: 12pF; C_0805_2012Metric; Voltage 50V; LCSC C1792
C111, C112: 100pF; C_0805_2012Metric; Voltage 50V; LCSC C1790
C114, C123, C124, C127: 10uF; C_0805_2012Metric; LCSC C15850
D101, D102, D103, D104, D105, D106, D107, D108: LED; LED_0805_1.15x1.40mm_HandSolder
FB101: Ferrite_Bead; FB_0805_2012Metric; LCSC C1017
G101: Logo_UFRGS_Large; Logo_UFRGS_22.0x12.0mm_Mask
G102: Logo_e-Power_Large; Logo_e-Power_22.8x12.0mm_SilkS
G103: Logo_UFRGS_Large; Logo_UFRGS_22.0x12.0mm_SilkS
G104: SYM_LASER_Large; WEEE-Logo_8.4x12mm_SilkScreen
G105: SYM_LASER_Large; KiCad-Logo_12mm_SilkScreen
G106: SYM_ESD_Large; ESD-Logo_13.2x12mm_SilkScreen
H101, H102, H103, H104: GND; MountingHole_3.2mm_M3_Pad_Via
J101: Conn_01x08_Male; Molex_Mini-Fit_Jr_2x04_P4.20mm_Horizontal
J102: ST-LINK; PinHeader_1x05_P2.54mm_Vertical
Q101: MMBT3904; SOT-23; LCSC C20526
R101, R102, R103, R105, R106, R107, R108, R119, R121, R126, R127, R128, R129, R130, R131, R132, R133, R137, R139, R147, R149: 1K; R_0805_2012Metric; Voltage 150V; LCSC C17513
R104, R109, R113, R114, R115, R116, R117, R118, R120, R122, R123, R124, R125, R134, R135, R136, R138, R140, R141, R142, R143, R144, R145, R146, R148, R150: 10K; R_0805_2012Metric; Voltage 150V; LCSC C17414
R110: 100R; R_0805_2012Metric; Voltage 150V; LCSC C17408
R111, R112: 10R; R_0805_2012Metric; Voltage 150V; LCSC C17415
SW101: SW_Push; SW_Push_1P1T_NO_6x6mm_H9.5mm
TP101: B1; TestPoint_Pad_D1.0mm
TP102: B2; TestPoint_Pad_D1.0mm
TP103: B3; TestPoint_Pad_D1.0mm
TP104: B4; TestPoint_Pad_D1.0mm
TP105: B5; TestPoint_Pad_D1.0mm
TP106: B6; TestPoint_Pad_D1.0mm
TP107: B7; TestPoint_Pad_D1.0mm
TP108: B8; TestPoint_Pad_D1.0mm
TP109: B9; TestPoint_Pad_D1.0mm
TP110: B10; TestPoint_Pad_D1.0mm
TP111: B11; TestPoint_Pad_D1.0mm
TP112: B12; TestPoint_Pad_D1.0mm
TP113: B13; TestPoint_Pad_D1.0mm
TP114: B14; TestPoint_Pad_D1.0mm
TP115: B15; TestPoint_Pad_D1.0mm
TP116: B16; TestPoint_Pad_D1.0mm
TP117: B17; TestPoint_Pad_D1.0mm
TP118: B18; TestPoint_Pad_D1.0mm
TP119: B19; TestPoint_Pad_D1.0mm
TP120: B20; TestPoint_Pad_D1.0mm
TP121: B21; TestPoint_Pad_D1.0mm
TP122: B22; TestPoint_Pad_D1.0mm
TP123: B23; TestPoint_Pad_D1.0mm
TP124: B24; TestPoint_Pad_D1.0mm
TP125, TP127, TP133, TP138: GND; TestPoint_Pad_D1.0mm
TP126, TP132: VCC; TestPoint_Pad_D1.0mm
TP128: CAN_L; TestPoint_Pad_D1.0mm
TP129: CAN_H; TestPoint_Pad_D1.0mm
TP130: CAN_GND; TestPoint_Pad_D1.0mm
TP131: ~ERROR; TestPoint_Pad_D1.0mm
TP134, TP161: T_SWCLK; TestPoint_Pad_D1.0mm
TP135, TP163: 3.3V; TestPoint_Pad_D1.0mm
TP136: NRST; TestPoint_Pad_D1.0mm
TP137, TP160: T_SWDIO; TestPoint_Pad_D1.0mm
TP139: VOUT_1P; TestPoint_Pad_D1.0mm
TP140: VOUT_2P; TestPoint_Pad_D1.0mm
TP141: VOUT_3P; TestPoint_Pad_D1.0mm
TP142: TOUT_1P; TestPoint_Pad_D1.0mm
TP143, TP159: ERROR_TRIG; TestPoint_Pad_D1.0mm
TP144, TP158: V_ERROR; TestPoint_Pad_D1.0mm
TP145, TP157: T_ERROR; TestPoint_Pad_D1.0mm
TP146, TP156: C_ERROR; TestPoint_Pad_D1.0mm
TP147: C1; TestPoint_Pad_D1.0mm
TP148: S; TestPoint_Pad_D1.0mm
TP149: S0; TestPoint_Pad_D1.0mm
TP150: S1; TestPoint_Pad_D1.0mm
TP151: S2; TestPoint_Pad_D1.0mm
TP152: TX; TestPoint_Pad_D1.0mm
TP153: TOUT_3P; TestPoint_Pad_D1.0mm
TP154: RX; TestPoint_Pad_D1.0mm
TP155: TOUT_2P; TestPoint_Pad_D1.0mm
TP162: PB3; TestPoint_Pad_D1.0mm
U101, U102, U103, U104, U105, U106: 74HC4051; SOP-16_4.4x10.4mm_P1.27mm; LCSC C9386
U107, U109, U111: 74HC595; SOP-16_4.4x10.4mm_P1.27mm; LCSC C5947
U108: STM32G431CBTx; LQFP-48_7x7mm_P0.5mm
U110: MCP2558; SOIC-8_3.9x4.9mm_P1.27mm
U112, U113: LM324; SOIC-14_3.9x8.7mm_P1.27mm; LCSC C71035
Y101: 24MHz; Crystal_HC52-6mm_Vertical
Y102: 32.768KHz; Crystal_HC52-6mm_Vertical

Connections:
+3V3: C119.1, C120.1, C121.1, C122.1, C123.1, C124.1, C127.1, FB101.1, J102.5, R133.1, TP135.1, TP163.1, U108.24 (VDD), U108.36 (VDD), U108.48 (VDD); also elsewhere on the board
+5V: C101.2, C102.2, C103.2, C104.2, C106.2, C107.2, C108.2, C113.2, C116.1, C118.2, C125.1, C126.1, U101.16 (VCC), U102.16 (VCC), U103.16 (VCC), U104.16 (VCC), U105.16 (VCC), U106.16 (VCC), U107.16 (VCC), U109.16 (VCC), U110.2 (VSS), U111.16 (VCC), U112.4 (V+), U113.4 (V+); also elsewhere on the board
/1.8V: C114.1, C115.1; also elsewhere on the board
/2.2727V: R114.2, R115.2, R124.2, R125.2, R142.2, R143.2; also elsewhere on the board
/B1: TP101.1, U107.15 (QA); also elsewhere on the board
/B2: TP102.1, U107.1 (QB); also elsewhere on the board
/B3: TP103.1, U107.2 (QC); also elsewhere on the board
/B4: TP104.1, U107.3 (QD); also elsewhere on the board
/B5: TP105.1, U107.4 (QE); also elsewhere on the board
/B6: TP106.1, U107.5 (QF); also elsewhere on the board
/B7: TP107.1, U107.6 (QG); also elsewhere on the board
/B8: TP108.1, U107.7 (QH); also elsewhere on the board
/B9: TP109.1, U109.15 (QA); also elsewhere on the board
/B10: TP110.1, U109.1 (QB); also elsewhere on the board
/B11: TP111.1, U109.2 (QC); also elsewhere on the board
/B12: TP112.1, U109.3 (QD); also elsewhere on the board
/B13: TP113.1, U109.4 (QE); also elsewhere on the board
/B14: TP114.1, U109.5 (QF); also elsewhere on the board
/B15: TP115.1, U109.6 (QG); also elsewhere on the board
/B16: TP116.1, U109.7 (QH); also elsewhere on the board
/B17: TP117.1, U111.15 (QA); also elsewhere on the board
/B18: TP118.1, U111.1 (QB); also elsewhere on the board
/B19: TP119.1, U111.2 (QC); also elsewhere on the board
/B20: TP120.1, U111.3 (QD); also elsewhere on the board
/B21: TP121.1, U111.4 (QE); also elsewhere on the board
/B22: TP122.1, U111.5 (QF); also elsewhere on the board
/B23: TP123.1, U111.6 (QG); also elsewhere on the board
/B24: TP124.1, U111.7 (QH); also elsewhere on the board
/C1: TP147.1, U108.17 (PB1); also elsewhere on the board
/CAN_H: J101.4, R112.2, TP129.1, U110.7 (CANH)
/CAN_L: J101.3, R110.2, TP128.1, U110.6 (CANL)
/C_ERROR: R126.1, TP146.1, TP156.1, U108.16 (PB0)
/DS: U107.14 (SER), U108.44 (PB7)
/ERROR_TRIG: R103.1, R104.1, R129.1, TP143.1, TP159.1, U108.13 (PA5)
/RCLK: U107.12 (RCLK), U108.41 (PB4), U109.12 (RCLK), U111.12 (RCLK)
/RX: TP154.1, U108.34 (PA12), U110.4 (RXD)
/S: TP148.1, U108.29 (PB15), U110.8 (S)
/S0: TP149.1, U101.11 (S0), U102.11 (S0), U103.11 (S0), U104.11 (S0), U105.11 (S0), U106.11 (S0), U108.30 (PA8)
/S1: TP150.1, U101.10 (S1), U102.10 (S1), U103.10 (S1), U104.10 (S1), U105.10 (S1), U106.10 (S1), U108.31 (PA9)
/S2: TP151.1, U101.9 (S2), U102.9 (S2), U103.9 (S2), U104.9 (S2), U105.9 (S2), U106.9 (S2), U108.32 (PA10)
/SCLK: U107.11 (SRCLK), U108.43 (PB6), U109.11 (SRCLK), U111.11 (SRCLK)
/T1: U105.13 (A0); also elsewhere on the board
/T2: U105.14 (A1); also elsewhere on the board
/T3: U105.15 (A2); also elsewhere on the board
/T4: U105.12 (A3); also elsewhere on the board
/T5: U105.1 (A4); also elsewhere on the board
/T6: U105.5 (A5); also elsewhere on the board
/T7: U105.2 (A6); also elsewhere on the board
/T8: U105.4 (A7); also elsewhere on the board
/T9: U103.13 (A0); also elsewhere on the board
/T10: U103.14 (A1); also elsewhere on the board
/T11: U103.15 (A2); also elsewhere on the board
/T12: U103.12 (A3); also elsewhere on the board
/T13: U103.1 (A4); also elsewhere on the board
/T14: U103.5 (A5); also elsewhere on the board
/T15: U103.2 (A6); also elsewhere on the board
/T16: U103.4 (A7); also elsewhere on the board
/T17: U101.13 (A0); also elsewhere on the board
/T18: U101.14 (A1); also elsewhere on the board
/T19: U101.15 (A2); also elsewhere on the board
/T20: U101.12 (A3); also elsewhere on the board
/T21: U101.1 (A4); also elsewhere on the board
/T22: U101.5 (A5); also elsewhere on the board
/T23: U101.2 (A6); also elsewhere on the board
/T24: U101.4 (A7); also elsewhere on the board
/TOUT_1: R116.2, R117.2, U105.3 (A)
/TOUT_1P: R113.1, TP142.1, U108.11 (PA3), U112.1
/TOUT_2: R134.2, R135.2, U103.3 (A)
/TOUT_2P: R123.1, TP155.1, U108.28 (PB14), U112.7
/TOUT_3: R144.2, R145.2, U101.3 (A)
/TOUT_3P: R141.1, TP153.1, U108.26 (PB12), U112.8
/TX: TP152.1, U108.33 (PA11), U110.1 (TXD)
/T_ERROR: R127.1, TP145.1, TP157.1, U108.15 (PA7)
/V1: U106.13 (A0); also elsewhere on the board
/V2: U106.14 (A1); also elsewhere on the board
/V3: U106.15 (A2); also elsewhere on the board
/V4: U106.12 (A3); also elsewhere on the board
/V5: U106.1 (A4); also elsewhere on the board
/V6: U106.5 (A5); also elsewhere on the board
/V7: U106.2 (A6); also elsewhere on the board
/V8: U106.4 (A7); also elsewhere on the board
/V9: U104.13 (A0); also elsewhere on the board
/V10: U104.14 (A1); also elsewhere on the board
/V11: U104.15 (A2); also elsewhere on the board
/V12: U104.12 (A3); also elsewhere on the board
/V13: U104.1 (A4); also elsewhere on the board
/V14: U104.5 (A5); also elsewhere on the board
/V15: U104.2 (A6); also elsewhere on the board
/V16: U104.4 (A7); also elsewhere on the board
/V17: U102.13 (A0); also elsewhere on the board
/V18: U102.14 (A1); also elsewhere on the board
/V19: U102.15 (A2); also elsewhere on the board
/V20: U102.12 (A3); also elsewhere on the board
/V21: U102.1 (A4); also elsewhere on the board
/V22: U102.5 (A5); also elsewhere on the board
/V23: U102.2 (A6); also elsewhere on the board
/V24: U102.4 (A7); also elsewhere on the board
/VCC: J101.1, J101.7, TP126.1, TP132.1; also elsewhere on the board
/VOUT_1: U106.3 (A), U113.3 (+)
/VOUT_1P: R120.1, R122.2, TP139.1, U108.8 (PA0), U113.1
/VOUT_2: U104.3 (A), U113.5 (+)
/VOUT_2P: R138.1, R140.2, TP140.1, U108.9 (PA1), U113.7
/VOUT_3: U102.3 (A), U113.10 (+)
/VOUT_3P: R148.1, R150.2, TP141.1, U108.10 (PA2), U113.8
/V_ERROR: R128.1, TP144.1, TP158.1, U108.14 (PA6)
/~ERROR: J101.6, Q101.3 (C), TP131.1
/~RESET: U107.10 (~SRCLR), U108.42 (PB5), U109.10 (~SRCLR), U111.10 (~SRCLR)
GND: C101.1, C102.1, C103.1, C104.1, C105.2, C106.1, C107.1, C108.1, C109.1, C110.1, C111.1, C112.1, C113.1, C114.2, C115.2, C116.2, C117.2, C118.1, C119.2, C120.2, C121.2, C122.2, C123.2, C124.2, C125.2, C126.2, C127.2, D101.1 (K), D102.1 (K), D103.1 (K), D104.1 (K), D105.1 (K), D106.1 (K), D107.1 (K), D108.1 (K), J101.2, J101.5, J101.8, J102.3, Q101.2 (E), R101.1, R102.1, R104.2, R105.1, R106.1, R107.1, R108.1, R109.2, R118.2, R121.1, R136.2, R139.1, R146.2, R149.1, SW101.1, TP125.1, TP127.1, TP130.1, TP133.1, TP138.1, U101.7 (VEE), U101.8 (GND), U102.7 (VEE), U102.8 (GND), U103.7 (VEE), U103.8 (GND), U104.7 (VEE), U104.8 (GND), U105.7 (VEE), U105.8 (GND), U106.7 (VEE), U106.8 (GND), U107.8 (GND), U108.19 (VSSA), U108.23 (VSS), U108.35 (VSS), U108.47 (VSS), U109.8 (GND), U110.3 (VDD), U111.8 (GND), U112.11 (V-), U113.11 (V-); also elsewhere on the board
NRST: C105.1, J102.1, SW101.2, TP136.1, U108.7 (PG10)
unnamed: C109.2, U108.5 (PF0), Y101.1
unnamed: C110.2, U108.6 (PF1), Y101.2
unnamed: C111.2, U108.4 (PC15), Y102.1
unnamed: C112.2, U108.3 (PC14), Y102.2
unnamed: C117.1, U110.5 (VIO)
unnamed: D101.2 (A), R126.2
unnamed: D102.2 (A), R127.2
unnamed: D103.2 (A), R128.2
unnamed: D104.2 (A), R129.2
unnamed: D105.2 (A), R130.2
unnamed: D106.2 (A), R131.2
unnamed: D107.2 (A), R132.2
unnamed: D108.2 (A), R133.2
unnamed: Q101.1 (B), R103.2
unnamed: R101.2, U101.6 (~E)
unnamed: R102.2, U102.6 (~E)
unnamed: R105.2, U103.6 (~E)
unnamed: R106.2, U104.6 (~E)
unnamed: R107.2, U105.6 (~E)
unnamed: R108.2, U106.6 (~E)
unnamed: R109.1, U108.45 (PB8)
unnamed: R110.1, R111.1
unnamed: R111.2, R112.1
unnamed: R113.2, R114.1, R115.1, U112.2 (-)
unnamed: R116.1, R117.1, R118.1, U112.3 (+)
unnamed: R119.1, R121.2
unnamed: R119.2, R120.2, R122.1, U113.2 (-)
unnamed: R123.2, R124.1, R125.1, U112.6 (-)
unnamed: R134.1, R135.1, R136.1, U112.5 (+)
unnamed: R137.1, R139.2
unnamed: R137.2, R138.2, R140.1, U113.6 (-)
unnamed: R141.2, R142.1, R143.1, U112.9 (-)
unnamed: R144.1, R145.1, R146.1, U112.10 (+)
unnamed: R147.1, R149.2
unnamed: R147.2, R148.2, R150.1, U113.9 (-)
unnamed: U107.9 (QH'), U109.14 (SER)
unnamed: U109.9 (QH'), U111.14 (SER)
PB3: R132.1, TP162.1, U107.13 (~OE), U108.40 (PB3), U109.13 (~OE), U111.13 (~OE)
T_SWCLK: J102.4, R131.1, TP134.1, TP161.1, U108.38 (PA14)
T_SWDIO: J102.2, R130.1, TP137.1, TP160.1, U108.37 (PA13)
VDDA: FB101.2, U108.20 (VREF+)

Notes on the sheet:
adicionar: - microcontrolador
1mV/5mV
(VS_1/5)*3.5
0.00V ~~ 4.20V
Gen. +12V, +5V, +3.3V
-45.9ºC ~~ 119.2ºC
0.000V ~~ 3.300V
(TS_1-2.2727V)*2
20mV/ºC
0.00V ~~ 2.94V


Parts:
C201, C204, C206, C207, C209, C211: 100nF; C_0805_2012Metric; Voltage 50V; LCSC C49678
C202, C203, C205, C208, C210: 10uF; C_0805_2012Metric; LCSC C15850
Q201: MMBT5401; SOT-23; LCSC C8326
R201, R210: 100R; R_0805_2012Metric; LCSC C17408
R202, R204, R206, R208, R212, R214, R215, R216, R217, R218, R219, R221, R225, R226, R228, R229: 1K; R_0805_2012Metric; Voltage 150V; LCSC C17513
R203, R209, R213, R220, R222, R223, R227: 0R; R_0805_2012Metric; LCSC C17477
R205, R207, R211: 100K; R_0805_2012Metric; LCSC C17407
R224, R230: 10K; R_0805_2012Metric; Voltage 150V; LCSC C17414
TP201: 1.8V; TestPoint_Pad_D1.0mm
TP202: 5.000V; TestPoint_Pad_D1.0mm
TP203: GND; TestPoint_Pad_D1.0mm
TP204: 0.850V; TestPoint_Pad_D1.0mm
TP205: 2.2727V; TestPoint_Pad_D1.0mm
U201: LM324; SOIC-14_3.9x8.7mm_P1.27mm; LCSC C71035
U202, U203, U204: TL431; SOT-23; LCSC C3113

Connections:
+5V: R201.1; also elsewhere on the board
+12V: C211.1, R204.2, R206.1, U201.4 (V+), U202.2 (K); also elsewhere on the board
/0.850V: R223.2, TP204.1; also elsewhere on the board
/1.8V: R203.1, TP201.1; also elsewhere on the board
/2.2727V: R227.2, TP205.1; also elsewhere on the board
/5.000V: R213.2, TP202.1; also elsewhere on the board
GND: C201.2, C202.2, C203.1, C204.1, C205.2, C206.2, C207.2, C208.2, C209.2, C210.2, C211.2, R202.2, R205.1, R207.1, R208.1, R212.1, R219.1, R221.1, R228.2, R230.1, TP203.1, U201.11 (V-), U203.3 (A), U204.3 (A); also elsewhere on the board
unnamed: C201.1, C202.1, R216.1, R217.2, U201.5 (+)
unnamed: C203.2, C204.2, Q201.3 (C), R226.2, U201.10 (+), U204.2 (K)
unnamed: C205.1, C206.1, R210.2, R216.2, R229.2, U203.1 (REF), U203.2 (K)
unnamed: C207.1, C208.1, R229.1, R230.2, U201.3 (+)
unnamed: C209.1, C210.1, R220.2, R225.2, U201.12 (+)
unnamed: Q201.1 (B), R214.2, R221.2, U202.3 (A)
unnamed: Q201.2 (E), R206.2
unnamed: R201.2, R210.1
unnamed: R202.1, R205.2, R209.2
unnamed: R203.2, U201.6 (-), U201.7
unnamed: R204.1, R214.1, U202.1 (REF)
unnamed: R207.2, R208.2, R211.2, R215.2, R220.1
unnamed: R209.1, R211.1, R215.1
unnamed: R212.2, R218.1, R219.2
unnamed: R213.1, R222.2, R224.2
unnamed: R217.1, R218.2
unnamed: R222.1, U201.8, U201.9 (-)
unnamed: R223.1, U201.13 (-), U201.14
unnamed: R224.1, R225.1
unnamed: R226.1, R228.1, U204.1 (REF)
unnamed: R227.1, U201.1, U201.2 (-)

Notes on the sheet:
2.5V
1.8V
2.2727V

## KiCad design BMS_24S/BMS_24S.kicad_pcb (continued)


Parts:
C301, C306, C309: 100nF; C_0805_2012Metric; Voltage 50V; LCSC C49678
C302: 10uF; C_0805_2012Metric; LCSC C15850
C303, C304, C305, C307, C308: 220uF; CP_Elec_10x10
D301: SS54HF; DO-214AC
D302: LED; LED_0805_1.15x1.40mm_HandSolder
F301: Fuse_1206; FUSE_1206_3216Metric
FB301, FB302, FB303, FB304, FB305, FB306, FB307, FB308, FB309, FB310: Ferrite_Bead; FB_0805_2012Metric; LCSC C1017
R301, R302, R303, R305, R306, R313: 1K; R_0805_2012Metric; Voltage 150V; LCSC C17513
R304, R314: ADJ; R_0805_2012Metric
R307, R308, R309, R310, R311, R312, R315, R316, R317: 1R; R_0805_2012Metric; Voltage 150V; LCSC C25271
TP301: +VIN; TestPoint_Pad_D1.0mm
TP302: +12V; TestPoint_Pad_D1.0mm
TP303, TP304: +5V; TestPoint_Pad_D1.0mm
TP305, TP306: +3.3V; TestPoint_Pad_D1.0mm
TP307: +C; TestPoint_Pad_D1.0mm
TP308: -C; TestPoint_Pad_D1.0mm
TP309, TP310: GND; TestPoint_Pad_D1.0mm
U301: LM317; TO-220-3_Horizontal_TabDown
U302: AP1117-33; SOT-223-3_TabPin2; LCSC C6186

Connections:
+3V3: C308.1, C309.1, TP305.1, TP306.1, U302.2 (VO); also elsewhere on the board
+5V: C305.1, C306.1, C307.1, R301.1, R302.1, R303.1, R304.1, R305.1, R306.1, TP303.1, TP304.1, U301.2 (VO), U302.3 (VI); also elsewhere on the board
+12V: C301.1, C302.1, C303.1, C304.1, R309.1, R312.1, R317.1, TP302.1, TP308.1, U301.3 (VI); also elsewhere on the board
/VCC: D301.2 (A); also elsewhere on the board
GND: C301.2, C302.2, C303.2, C304.2, C305.2, C306.2, C307.2, C308.2, C309.2, D302.1 (K), FB302.2, FB310.1, R313.2, R314.2, TP309.1, TP310.1, U302.1 (GND); also elsewhere on the board
unnamed: D301.1 (K), F301.2
unnamed: D302.2 (A), R305.2, R306.2
unnamed: F301.1, FB301.2
unnamed: FB301.1, R307.2, R310.2, R315.2, TP301.1, TP307.1
unnamed: FB302.1, FB303.1
unnamed: FB303.2, FB304.2
unnamed: FB304.1, FB305.1
unnamed: FB305.2, FB306.2
unnamed: FB306.1, FB307.1
unnamed: FB307.2, FB308.2
unnamed: FB308.1, FB309.1
unnamed: FB309.2, FB310.2
unnamed: R301.2, R302.2, R303.2, R304.2, R313.1, R314.1, U301.1 (ADJ)
unnamed: R307.1, R308.2, R310.1, R311.2, R315.1, R316.2
unnamed: R308.1, R309.2, R311.1, R312.2, R316.1, R317.2

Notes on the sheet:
Vref = 1.25V
C = V


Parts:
F401, F402, F403, F404, F405, F406, F407, F408, F409, F410, F411, F412, F413, F414, F415, F416, F417, F418, F419, F420, F421, F422, F423, F424, F425, F426: Fuse; FUSE_1206_3216Metric
J401: VOLT_IDC_26_CONN; IDC-Header_2x13_P2.54mm_Horizontal

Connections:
CELL_1: F420.2; also elsewhere on the board
CELL_2: F418.2; also elsewhere on the board
CELL_3: F416.2; also elsewhere on the board
CELL_4: F414.2; also elsewhere on the board
CELL_5: F423.2; also elsewhere on the board
CELL_6: F425.2; also elsewhere on the board
CELL_7: F426.2; also elsewhere on the board
CELL_8: F424.2; also elsewhere on the board
CELL_9: F415.2; also elsewhere on the board
CELL_10: F417.2; also elsewhere on the board
CELL_11: F419.2; also elsewhere on the board
CELL_12: F421.2; also elsewhere on the board
CELL_13: F407.2; also elsewhere on the board
CELL_14: F409.2; also elsewhere on the board
CELL_15: F411.2; also elsewhere on the board
CELL_16: F413.2; also elsewhere on the board
CELL_17: F402.2; also elsewhere on the board
CELL_18: F401.2; also elsewhere on the board
CELL_19: F403.2; also elsewhere on the board
CELL_20: F405.2; also elsewhere on the board
CELL_21: F410.2; also elsewhere on the board
CELL_22: F408.2; also elsewhere on the board
CELL_23: F406.2; also elsewhere on the board
CELL_24: F404.2; also elsewhere on the board
CELL_GND: F422.2; also elsewhere on the board
unnamed: F401.1, J401.1
unnamed: F402.1, J401.2
unnamed: F403.1, J401.3
unnamed: F404.1, J401.4
unnamed: F405.1, J401.5
unnamed: F406.1, J401.6
unnamed: F407.1, J401.7
unnamed: F408.1, J401.8
unnamed: F409.1, J401.9
unnamed: F410.1, J401.10
unnamed: F411.1, J401.11
unnamed: F412.1, J401.12
unnamed: F413.1, J401.13
unnamed: F414.1, J401.14
unnamed: F415.1, J401.15
unnamed: F416.1, J401.16
unnamed: F417.1, J401.17
unnamed: F418.1, J401.18
unnamed: F419.1, J401.19
unnamed: F420.1, J401.20
unnamed: F421.1, J401.21
unnamed: F422.1, J401.22
unnamed: F423.1, J401.23
unnamed: F424.1, J401.24
unnamed: F425.1, J401.25
unnamed: F426.1, J401.26


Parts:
J1701: TEMP_IDC_26_CONN; IDC-Header_2x13_P2.54mm_Horizontal
R1701, R1702, R1703, R1704, R1705, R1706, R1707, R1708, R1709, R1710, R1711, R1712, R1713, R1714, R1715, R1716, R1717, R1718, R1719, R1720, R1721, R1722, R1723, R1724, R1725, R1726: 0R; R_0805_2012Metric; LCSC C17477

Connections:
/Temperature Sensors/0V: R1701.2, R1702.2
/Temperature Sensors/TS_1: R1725.2; also elsewhere on the board
/Temperature Sensors/TS_2: R1726.2; also elsewhere on the board
/Temperature Sensors/TS_3: R1715.2; also elsewhere on the board
/Temperature Sensors/TS_4: R1716.2; also elsewhere on the board
/Temperature Sensors/TS_5: R1723.2; also elsewhere on the board
/Temperature Sensors/TS_6: R1724.2; also elsewhere on the board
/Temperature Sensors/TS_7: R1717.2; also elsewhere on the board
/Temperature Sensors/TS_8: R1718.2; also elsewhere on the board
/Temperature Sensors/TS_9: R1721.2; also elsewhere on the board
/Temperature Sensors/TS_10: R1722.2; also elsewhere on the board
/Temperature Sensors/TS_11: R1719.2; also elsewhere on the board
/Temperature Sensors/TS_12: R1720.2; also elsewhere on the board
/Temperature Sensors/TS_13: R1713.2; also elsewhere on the board
/Temperature Sensors/TS_14: R1714.2; also elsewhere on the board
/Temperature Sensors/TS_15: R1703.2; also elsewhere on the board
/Temperature Sensors/TS_16: R1704.2; also elsewhere on the board
/Temperature Sensors/TS_17: R1711.2; also elsewhere on the board
/Temperature Sensors/TS_18: R1712.2; also elsewhere on the board
/Temperature Sensors/TS_19: R1705.2; also elsewhere on the board
/Temperature Sensors/TS_20: R1706.2; also elsewhere on the board
/Temperature Sensors/TS_21: R1709.2; also elsewhere on the board
/Temperature Sensors/TS_22: R1710.2; also elsewhere on the board
/Temperature Sensors/TS_23: R1707.2; also elsewhere on the board
/Temperature Sensors/TS_24: R1708.2; also elsewhere on the board
unnamed: J1701.1, R1701.1
unnamed: J1701.2, R1702.1
unnamed: J1701.3, R1703.1
unnamed: J1701.4, R1704.1
unnamed: J1701.5, R1705.1
unnamed: J1701.6, R1706.1
unnamed: J1701.7, R1707.1
unnamed: J1701.8, R1708.1
unnamed: J1701.9, R1709.1
unnamed: J1701.10, R1710.1
unnamed: J1701.11, R1711.1
unnamed: J1701.12, R1712.1
unnamed: J1701.13, R1713.1
unnamed: J1701.14, R1714.1
unnamed: J1701.15, R1715.1
unnamed: J1701.16, R1716.1
unnamed: J1701.17, R1717.1
unnamed: J1701.18, R1718.1
unnamed: J1701.19, R1719.1
unnamed: J1701.20, R1720.1
unnamed: J1701.21, R1721.1
unnamed: J1701.22, R1722.1
unnamed: J1701.23, R1723.1
unnamed: J1701.24, R1724.1
unnamed: J1701.25, R1725.1
unnamed: J1701.26, R1726.1


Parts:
C3101: 100nF; C_0805_2012Metric; Voltage 50V; LCSC C49678
J3101: Current_Conn; PinHeader_1x04_P2.54mm_Horizontal
J3102: BSPD_Conn; PinHeader_1x04_P2.54mm_Horizontal
JP3101: Jumper; SolderJumper-2_P1.3mm_Open_TrianglePad1.0x1.5mm
R3101: 0R; R_0805_2012Metric; Voltage 150V; LCSC C17477
R3102, R3103, R3104, R3105: 10K; R_0805_2012Metric; Voltage 150V; LCSC C17414
U3101: LM324; SOIC-14_3.9x8.7mm_P1.27mm; LCSC C71035

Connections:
+5V: C3101.1, U3101.4 (V+); also elsewhere on the board
/0.850V: R3103.2; also elsewhere on the board
/5.000V: R3101.1; also elsewhere on the board
/C1: R3102.2, U3101.8; also elsewhere on the board
/Current Sensor/BSPD_SIG: J3102.1, U3101.6 (-), U3101.7
/Current Sensor/VCC: J3101.1, JP3101.1
/Current Sensor/VIOUT: J3101.3, U3101.3 (+), U3101.5 (+)
GND: C3101.2, J3101.2, J3102.2, R3105.1, U3101.11 (V-); also elsewhere on the board
unnamed: JP3101.2, R3101.2
unnamed: R3102.1, R3103.1, U3101.9 (-)
unnamed: R3104.1, R3105.2, U3101.10 (+)
unnamed: R3104.2, U3101.1, U3101.2 (-)

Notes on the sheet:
ACS758ECB-200B-PSS-T +-200A 10mV/A
1.650V ~~ 0.00A 10mV/A


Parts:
C501, C502, C503: 100nF; C_0805_2012Metric; Voltage 50V; LCSC C49678
D501, D502, D503, D504, D505, D506: LL4148; SOD-80; LCSC C9808
JP501, JP502, JP503: 0R; zero_ohm_resistor_0805; Voltage 150V
R501, R502, R503, R504, R505, R506, R507, R508, R509, R510, R511, R512, R513, R514, R515, R516: 1K; R_0805_2012Metric; Voltage 150V; LCSC C17513
U501, U503: TS1851ILT; SOT-23-5_HandSoldering
U502: TLP290-4; SOIC-16_4.55x10.3mm_P1.27mm(TLP290-4); LCSC C39031

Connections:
/1.8V: C501.1, U502.10, U502.14; also elsewhere on the board
/V1: C503.1, R516.2, U502.9; also elsewhere on the board
/V2: C502.1, R508.2, U502.13; also elsewhere on the board
CELL_1: D503.1 (K), R506.2, R509.2, R513.2, U501.2 (V-), U503.5 (V+); also elsewhere on the board
CELL_2: JP501.1, R501.2, R505.2, U501.5 (V+); also elsewhere on the board
CELL_GND: D506.1 (K), JP503.1, R514.2, U503.2 (V-); also elsewhere on the board
GND: C501.2, C502.2, C503.2, JP502.1, R507.1, R508.1, R515.1, R516.1; also elsewhere on the board
unnamed: D501.1 (K), D502.2 (A)
unnamed: D501.2 (A), R505.1, U502.16
unnamed: D502.1 (K), D503.2 (A)
unnamed: D504.1 (K), D505.2 (A)
unnamed: D504.2 (A), R513.1, U502.12
unnamed: D505.1 (K), D506.2 (A)
unnamed: R501.1, R502.2
unnamed: R502.1, R503.2
unnamed: R503.1, R504.2
unnamed: R504.1, R506.1, U501.3 (+)
unnamed: R507.2, U501.4 (-), U502.15
unnamed: R509.1, R510.2
unnamed: R510.1, R511.2
unnamed: R511.1, R512.2
unnamed: R512.1, R514.1, U503.3 (+)
unnamed: R515.2, U502.11, U503.4 (-)
unnamed: U501.1, U502.1, U502.3
unnamed: U502.2, U502.4
unnamed: U502.5, U502.7, U503.1
unnamed: U502.6, U502.8

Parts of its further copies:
C601, C602, C603, C701, C702, C703, C801, C802, C803, C901, C902, C903, C1001, C1002, C1003, C1101, C1102, C1103, C1201, C1202, C1203, C1301, C1302, C1303, C1401, C1402, C1403, C1501, C1502, C1503, C1601, C1602, C1603: 100nF; C_0805_2012Metric; Voltage 50V; LCSC C49678
D601, D602, D603, D604, D605, D606, D701, D702, D703, D704, D705, D706, D801, D802, D803, D804, D805, D806, D901, D902, D903, D904, D905, D906, D1001, D1002, D1003, D1004, D1005, D1006, D1101, D1102, D1103, D1104, D1105, D1106, D1201, D1202, D1203, D1204, D1205, D1206, D1301, D1302, D1303, D1304, D1305, D1306, D1401, D1402, D1403, D1404, D1405, D1406, D1501, D1502, D1503, D1504, D1505, D1506, D1601, D1602, D1603, D1604, D1605, D1606: LL4148; SOD-80; LCSC C9808
JP601, JP602, JP603, JP701, JP702, JP703, JP801, JP802, JP803, JP901, JP902, JP903, JP1001, JP1002, JP1003, JP1101, JP1102, JP1103, JP1201, JP1202, JP1203, JP1301, JP1302, JP1303, JP1401, JP1402, JP1403, JP1501, JP1502, JP1503, JP1601, JP1602, JP1603: 0R; zero_ohm_resistor_0805; Voltage 150V
R601, R602, R603, R604, R605, R606, R607, R608, R609, R610, R611, R612, R613, R614, R615, R616, R701, R702, R703, R704, R705, R706, R707, R708, R709, R710, R711, R712, R713, R714, R715, R716, R801, R802, R803, R804, R805, R806, R807, R808, R809, R810, R811, R812, R813, R814, R815, R816, R901, R902, R903, R904, R905, R906, R907, R908, R909, R910, R911, R912, R913, R914, R915, R916, R1001, R1002, R1003, R1004, R1005, R1006, R1007, R1008, R1009, R1010, R1011, R1012, R1013, R1014, R1015, R1016, R1101, R1102, R1103, R1104, R1105, R1106, R1107, R1108, R1109, R1110, R1111, R1112, R1113, R1114, R1115, R1116, R1201, R1202, R1203, R1204, R1205, R1206, R1207, R1208, R1209, R1210, R1211, R1212, R1213, R1214, R1215, R1216, R1301, R1302, R1303, R1304, R1305, R1306, R1307, R1308, R1309, R1310, R1311, R1312, R1313, R1314, R1315, R1316, R1401, R1402, R1403, R1404, R1405, R1406, R1407, R1408, R1409, R1410, R1411, R1412, R1413, R1414, R1415, R1416, R1501, R1502, R1503, R1504, R1505, R1506, R1507, R1508, R1509, R1510, R1511, R1512, R1513, R1514, R1515, R1516, R1601, R1602, R1603, R1604, R1605, R1606, R1607, R1608, R1609, R1610, R1611, R1612, R1613, R1614, R1615, R1616: 1K; R_0805_2012Metric; Voltage 150V; LCSC C17513
U601, U603, U701, U703, U801, U803, U901, U903, U1001, U1003, U1101, U1103, U1201, U1203, U1301, U1303, U1401, U1403, U1501, U1503, U1601, U1603: TS1851ILT; SOT-23-5_HandSoldering
U602, U702, U802, U902, U1002, U1102, U1202, U1302, U1402, U1502, U1602: TLP290-4; SOIC-16_4.55x10.3mm_P1.27mm(TLP290-4); LCSC C39031

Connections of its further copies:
/1.8V: C601.1, C701.1, C801.1, C901.1, C1001.1, C1101.1, C1201.1, C1301.1, C1401.1, C1501.1, C1601.1, U602.10, U602.14, U702.10, U702.14, U802.10, U802.14, U902.10, U902.14, U1002.10, U1002.14, U1102.10, U1102.14, U1202.10, U1202.14, U1302.10, U1302.14, U1402.10, U1402.14, U1502.10, U1502.14, U1602.10, U1602.14; also elsewhere on the board
/V3: C603.1, R616.2, U602.9; also elsewhere on the board
/V4: C602.1, R608.2, U602.13; also elsewhere on the board
/V5: C703.1, R716.2, U702.9; also elsewhere on the board
/V6: C702.1, R708.2, U702.13; also elsewhere on the board
/V7: C803.1, R816.2, U802.9; also elsewhere on the board
/V8: C802.1, R808.2, U802.13; also elsewhere on the board
/V9: C903.1, R916.2, U902.9; also elsewhere on the board
/V10: C902.1, R908.2, U902.13; also elsewhere on the board
/V11: C1003.1, R1016.2, U1002.9; also elsewhere on the board
/V12: C1002.1, R1008.2, U1002.13; also elsewhere on the board
/V13: C1103.1, R1116.2, U1102.9; also elsewhere on the board
/V14: C1102.1, R1108.2, U1102.13; also elsewhere on the board
/V15: C1203.1, R1216.2, U1202.9; also elsewhere on the board
/V16: C1202.1, R1208.2, U1202.13; also elsewhere on the board
/V17: C1303.1, R1316.2, U1302.9; also elsewhere on the board
/V18: C1302.1, R1308.2, U1302.13; also elsewhere on the board
/V19: C1403.1, R1416.2, U1402.9; also elsewhere on the board
/V20: C1402.1, R1408.2, U1402.13; also elsewhere on the board
/V21: C1503.1, R1516.2, U1502.9; also elsewhere on the board
/V22: C1502.1, R1508.2, U1502.13; also elsewhere on the board
/V23: C1603.1, R1616.2, U1602.9; also elsewhere on the board
/V24: C1602.1, R1608.2, U1602.13; also elsewhere on the board
CELL_2: D606.1 (K), JP603.1, R614.2, U603.2 (V-); also elsewhere on the board
CELL_3: D603.1 (K), R606.2, R609.2, R613.2, U601.2 (V-), U603.5 (V+); also elsewhere on the board
CELL_4: D706.1 (K), JP601.1, JP703.1, R601.2, R605.2, R714.2, U601.5 (V+), U703.2 (V-); also elsewhere on the board
CELL_5: D703.1 (K), R706.2, R709.2, R713.2, U701.2 (V-), U703.5 (V+); also elsewhere on the board
CELL_6: D806.1 (K), JP701.1, JP803.1, R701.2, R705.2, R814.2, U701.5 (V+), U803.2 (V-); also elsewhere on the board
CELL_7: D803.1 (K), R806.2, R809.2, R813.2, U801.2 (V-), U803.5 (V+); also elsewhere on the board
CELL_8: D906.1 (K), JP801.1, JP903.1, R801.2, R805.2, R914.2, U801.5 (V+), U903.2 (V-); also elsewhere on the board
CELL_9: D903.1 (K), R906.2, R909.2, R913.2, U901.2 (V-), U903.5 (V+); also elsewhere on the board
CELL_10: D1006.1 (K), JP901.1, JP1003.1, R901.2, R905.2, R1014.2, U901.5 (V+), U1003.2 (V-); also elsewhere on the board
CELL_11: D1003.1 (K), R1006.2, R1009.2, R1013.2, U1001.2 (V-), U1003.5 (V+); also elsewhere on the board
CELL_12: D1106.1 (K), JP1001.1, JP1103.1, R1001.2, R1005.2, R1114.2, U1001.5 (V+), U1103.2 (V-); also elsewhere on the board
CELL_13: D1103.1 (K), R1106.2, R1109.2, R1113.2, U1101.2 (V-), U1103.5 (V+); also elsewhere on the board
CELL_14: D1206.1 (K), JP1101.1, JP1203.1, R1101.2, R1105.2, R1214.2, U1101.5 (V+), U1203.2 (V-); also elsewhere on the board
CELL_15: D1203.1 (K), R1206.2, R1209.2, R1213.2, U1201.2 (V-), U1203.5 (V+); also elsewhere on the board
CELL_16: D1306.1 (K), JP1201.1, JP1303.1, R1201.2, R1205.2, R1314.2, U1201.5 (V+), U1303.2 (V-); also elsewhere on the board
CELL_17: D1303.1 (K), R1306.2, R1309.2, R1313.2, U1301.2 (V-), U1303.5 (V+); also elsewhere on the board
CELL_18: D1406.1 (K), JP1301.1, JP1403.1, R1301.2, R1305.2, R1414.2, U1301.5 (V+), U1403.2 (V-); also elsewhere on the board
CELL_19: D1403.1 (K), R1406.2, R1409.2, R1413.2, U1401.2 (V-), U1403.5 (V+); also elsewhere on the board
CELL_20: D1506.1 (K), JP1401.1, JP1503.1, R1401.2, R1405.2, R1514.2, U1401.5 (V+), U1503.2 (V-); also elsewhere on the board
CELL_21: D1503.1 (K), R1506.2, R1509.2, R1513.2, U1501.2 (V-), U1503.5 (V+); also elsewhere on the board
CELL_22: D1606.1 (K), JP1501.1, JP1603.1, R1501.2, R1505.2, R1614.2, U1501.5 (V+), U1603.2 (V-); also elsewhere on the board
CELL_23: D1603.1 (K), R1606.2, R1609.2, R1613.2, U1601.2 (V-), U1603.5 (V+); also elsewhere on the board
CELL_24: JP1601.1, R1601.2, R1605.2, U1601.5 (V+); also elsewhere on the board
GND: C601.2, C602.2, C603.2, C701.2, C702.2, C703.2, C801.2, C802.2, C803.2, C901.2, C902.2, C903.2, C1001.2, C1002.2, C1003.2, C1101.2, C1102.2, C1103.2, C1201.2, C1202.2, C1203.2, C1301.2, C1302.2, C1303.2, C1401.2, C1402.2, C1403.2, C1501.2, C1502.2, C1503.2, C1601.2, C1602.2, C1603.2, JP602.1, JP702.1, JP802.1, JP902.1, JP1002.1, JP1102.1, JP1202.1, JP1302.1, JP1402.1, JP1502.1, JP1602.1, R607.1, R608.1, R615.1, R616.1, R707.1, R708.1, R715.1, R716.1, R807.1, R808.1, R815.1, R816.1, R907.1, R908.1, R915.1, R916.1, R1007.1, R1008.1, R1015.1, R1016.1, R1107.1, R1108.1, R1115.1, R1116.1, R1207.1, R1208.1, R1215.1, R1216.1, R1307.1, R1308.1, R1315.1, R1316.1, R1407.1, R1408.1, R1415.1, R1416.1, R1507.1, R1508.1, R1515.1, R1516.1, R1607.1, R1608.1, R1615.1, R1616.1; also elsewhere on the board
unnamed: D601.1 (K), D602.2 (A)
unnamed: D601.2 (A), R605.1, U602.16
unnamed: D602.1 (K), D603.2 (A)
unnamed: D604.1 (K), D605.2 (A)
unnamed: D604.2 (A), R613.1, U602.12
unnamed: D605.1 (K), D606.2 (A)
unnamed: D701.1 (K), D702.2 (A)
unnamed: D701.2 (A), R705.1, U702.16
unnamed: D702.1 (K), D703.2 (A)
unnamed: D704.1 (K), D705.2 (A)
unnamed: D704.2 (A), R713.1, U702.12
unnamed: D705.1 (K), D706.2 (A)
unnamed: D801.1 (K), D802.2 (A)
unnamed: D801.2 (A), R805.1, U802.16
unnamed: D802.1 (K), D803.2 (A)
unnamed: D804.1 (K), D805.2 (A)
unnamed: D804.2 (A), R813.1, U802.12
unnamed: D805.1 (K), D806.2 (A)
unnamed: D901.1 (K), D902.2 (A)
unnamed: D901.2 (A), R905.1, U902.16
unnamed: D902.1 (K), D903.2 (A)
unnamed: D904.1 (K), D905.2 (A)
unnamed: D904.2 (A), R913.1, U902.12
unnamed: D905.1 (K), D906.2 (A)
unnamed: D1001.1 (K), D1002.2 (A)
unnamed: D1001.2 (A), R1005.1, U1002.16
unnamed: D1002.1 (K), D1003.2 (A)
unnamed: D1004.1 (K), D1005.2 (A)
unnamed: D1004.2 (A), R1013.1, U1002.12
unnamed: D1005.1 (K), D1006.2 (A)
unnamed: D1101.1 (K), D1102.2 (A)
unnamed: D1101.2 (A), R1105.1, U1102.16
unnamed: D1102.1 (K), D1103.2 (A)
unnamed: D1104.1 (K), D1105.2 (A)
unnamed: D1104.2 (A), R1113.1, U1102.12
unnamed: D1105.1 (K), D1106.2 (A)
unnamed: D1201.1 (K), D1202.2 (A)
unnamed: D1201.2 (A), R1205.1, U1202.16
unnamed: D1202.1 (K), D1203.2 (A)
unnamed: D1204.1 (K), D1205.2 (A)
unnamed: D1204.2 (A), R1213.1, U1202.12
unnamed: D1205.1 (K), D1206.2 (A)
unnamed: D1301.1 (K), D1302.2 (A)
unnamed: D1301.2 (A), R1305.1, U1302.16
unnamed: D1302.1 (K), D1303.2 (A)
unnamed: D1304.1 (K), D1305.2 (A)
unnamed: D1304.2 (A), R1313.1, U1302.12
unnamed: D1305.1 (K), D1306.2 (A)
unnamed: D1401.1 (K), D1402.2 (A)
unnamed: D1401.2 (A), R1405.1, U1402.16
unnamed: D1402.1 (K), D1403.2 (A)
unnamed: D1404.1 (K), D1405.2 (A)
unnamed: D1404.2 (A), R1413.1, U1402.12
unnamed: D1405.1 (K), D1406.2 (A)
unnamed: D1501.1 (K), D1502.2 (A)
unnamed: D1501.2 (A), R1505.1, U1502.16
unnamed: D1502.1 (K), D1503.2 (A)
unnamed: D1504.1 (K), D1505.2 (A)
unnamed: D1504.2 (A), R1513.1, U1502.12
unnamed: D1505.1 (K), D1506.2 (A)
unnamed: D1601.1 (K), D1602.2 (A)
unnamed: D1601.2 (A), R1605.1, U1602.16
unnamed: D1602.1 (K), D1603.2 (A)
unnamed: D1604.1 (K), D1605.2 (A)
unnamed: D1604.2 (A), R1613.1, U1602.12
unnamed: D1605.1 (K), D1606.2 (A)
unnamed: R601.1, R602.2
unnamed: R602.1, R603.2
unnamed: R603.1, R604.2
unnamed: R604.1, R606.1, U601.3 (+)
unnamed: R607.2, U601.4 (-), U602.15
unnamed: R609.1, R610.2
unnamed: R610.1, R611.2
unnamed: R611.1, R612.2
unnamed: R612.1, R614.1, U603.3 (+)
unnamed: R615.2, U602.11, U603.4 (-)
unnamed: R701.1, R702.2
unnamed: R702.1, R703.2
unnamed: R703.1, R704.2
unnamed: R704.1, R706.1, U701.3 (+)
unnamed: R707.2, U701.4 (-), U702.15
unnamed: R709.1, R710.2
unnamed: R710.1, R711.2
unnamed: R711.1, R712.2
unnamed: R712.1, R714.1, U703.3 (+)
unnamed: R715.2, U702.11, U703.4 (-)
unnamed: R801.1, R802.2
unnamed: R802.1, R803.2
unnamed: R803.1, R804.2
unnamed: R804.1, R806.1, U801.3 (+)
unnamed: R807.2, U801.4 (-), U802.15
unnamed: R809.1, R810.2
unnamed: R810.1, R811.2
unnamed: R811.1, R812.2
unnamed: R812.1, R814.1, U803.3 (+)
unnamed: R815.2, U802.11, U803.4 (-)
unnamed: R901.1, R902.2
unnamed: R902.1, R903.2
unnamed: R903.1, R904.2
unnamed: R904.1, R906.1, U901.3 (+)
unnamed: R907.2, U901.4 (-), U902.15
unnamed: R909.1, R910.2
unnamed: R910.1, R911.2
unnamed: R911.1, R912.2
unnamed: R912.1, R914.1, U903.3 (+)
unnamed: R915.2, U902.11, U903.4 (-)
unnamed: R1001.1, R1002.2
unnamed: R1002.1, R1003.2
unnamed: R1003.1, R1004.2
unnamed: R1004.1, R1006.1, U1001.3 (+)
unnamed: R1007.2, U1001.4 (-), U1002.15
unnamed: R1009.1, R1010.2
unnamed: R1010.1, R1011.2
unnamed: R1011.1, R1012.2
unnamed: R1012.1, R1014.1, U1003.3 (+)
unnamed: R1015.2, U1002.11, U1003.4 (-)
unnamed: R1101.1, R1102.2
unnamed: R1102.1, R1103.2
unnamed: R1103.1, R1104.2
unnamed: R1104.1, R1106.1, U1101.3 (+)
unnamed: R1107.2, U1101.4 (-), U1102.15
unnamed: R1109.1, R1110.2
unnamed: R1110.1, R1111.2
unnamed: R1111.1, R1112.2
unnamed: R1112.1, R1114.1, U1103.3 (+)
unnamed: R1115.2, U1102.11, U1103.4 (-)
unnamed: R1201.1, R1202.2
unnamed: R1202.1, R1203.2
unnamed: R1203.1, R1204.2
unnamed: R1204.1, R1206.1, U1201.3 (+)
unnamed: R1207.2, U1201.4 (-), U1202.15
unnamed: R1209.1, R1210.2
unnamed: R1210.1, R1211.2
unnamed: R1211.1, R1212.2
unnamed: R1212.1, R1214.1, U1203.3 (+)
unnamed: R1215.2, U1202.11, U1203.4 (-)
unnamed: R1301.1, R1302.2
unnamed: R1302.1, R1303.2
unnamed: R1303.1, R1304.2
unnamed: R1304.1, R1306.1, U1301.3 (+)
unnamed: R1307.2, U1301.4 (-), U1302.15
unnamed: R1309.1, R1310.2
unnamed: R1310.1, R1311.2
unnamed: R1311.1, R1312.2
unnamed: R1312.1, R1314.1, U1303.3 (+)
unnamed: R1315.2, U1302.11, U1303.4 (-)
unnamed: R1401.1, R1402.2
unnamed: R1402.1, R1403.2
unnamed: R1403.1, R1404.2
unnamed: R1404.1, R1406.1, U1401.3 (+)
unnamed: R1407.2, U1401.4 (-), U1402.15
unnamed: R1409.1, R1410.2
unnamed: R1410.1, R1411.2
unnamed: R1411.1, R1412.2
unnamed: R1412.1, R1414.1, U1403.3 (+)
unnamed: R1415.2, U1402.11, U1403.4 (-)
unnamed: R1501.1, R1502.2
unnamed: R1502.1, R1503.2
unnamed: R1503.1, R1504.2
unnamed: R1504.1, R1506.1, U1501.3 (+)
unnamed: R1507.2, U1501.4 (-), U1502.15
unnamed: R1509.1, R1510.2
unnamed: R1510.1, R1511.2
unnamed: R1511.1, R1512.2
unnamed: R1512.1, R1514.1, U1503.3 (+)
unnamed: R1515.2, U1502.11, U1503.4 (-)
unnamed: R1601.1, R1602.2
unnamed: R1602.1, R1603.2
unnamed: R1603.1, R1604.2
unnamed: R1604.1, R1606.1, U1601.3 (+)
unnamed: R1607.2, U1601.4 (-), U1602.15
unnamed: R1609.1, R1610.2
unnamed: R1610.1, R1611.2
unnamed: R1611.1, R1612.2
unnamed: R1612.1, R1614.1, U1603.3 (+)
unnamed: R1615.2, U1602.11, U1603.4 (-)
unnamed: U601.1, U602.1, U602.3
unnamed: U602.2, U602.4
unnamed: U602.5, U602.7, U603.1
unnamed: U602.6, U602.8
unnamed: U701.1, U702.1, U702.3
unnamed: U702.2, U702.4
unnamed: U702.5, U702.7, U703.1
unnamed: U702.6, U702.8
unnamed: U801.1, U802.1, U802.3
unnamed: U802.2, U802.4
unnamed: U802.5, U802.7, U803.1
unnamed: U802.6, U802.8
unnamed: U901.1, U902.1, U902.3
unnamed: U902.2, U902.4
unnamed: U902.5, U902.7, U903.1
unnamed: U902.6, U902.8
unnamed: U1001.1, U1002.1, U1002.3
unnamed: U1002.2, U1002.4
unnamed: U1002.5, U1002.7, U1003.1
unnamed: U1002.6, U1002.8
unnamed: U1101.1, U1102.1, U1102.3
unnamed: U1102.2, U1102.4
unnamed: U1102.5, U1102.7, U1103.1
unnamed: U1102.6, U1102.8
unnamed: U1201.1, U1202.1, U1202.3
unnamed: U1202.2, U1202.4
unnamed: U1202.5, U1202.7, U1203.1
unnamed: U1202.6, U1202.8
unnamed: U1301.1, U1302.1, U1302.3
unnamed: U1302.2, U1302.4
unnamed: U1302.5, U1302.7, U1303.1
unnamed: U1302.6, U1302.8
unnamed: U1401.1, U1402.1, U1402.3
unnamed: U1402.2, U1402.4
unnamed: U1402.5, U1402.7, U1403.1
unnamed: U1402.6, U1402.8
unnamed: U1501.1, U1502.1, U1502.3
unnamed: U1502.2, U1502.4
unnamed: U1502.5, U1502.7, U1503.1
unnamed: U1502.6, U1502.8
unnamed: U1601.1, U1602.1, U1602.3
unnamed: U1602.2, U1602.4
unnamed: U1602.5, U1602.7, U1603.1
unnamed: U1602.6, U1602.8

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

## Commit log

2020-07-19 adicionei a pasta do BMS ao repositorio
    [ACS758.sch, BMS_20S.csv, BMS_20S.kicad_pcb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]
2020-07-19 add current sense block to the schematic
    [BMS_20S.sch, LM235_1_2.sch, balancing.sch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]
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2020-07-21 adicionar o circuito do TSAL ao GIT
    [TSAL.csv, TSAL.kicad_pcb, TSAL.sch]
2020-07-22 add e-Power_conventions file
    [BMS_20S.kicad_pcb, e-Power_conventions.kicad_pcb]
2020-07-22 added other PCB projects to git repository
    [BMS_Eeschema.sch, BSPD_Eeschema.sch, BUCK-BOOST KiCad.csv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]
2020-07-23 added rounded corners to conventions
    [e-Power_conventions.kicad_pcb]
2020-07-23 rounded corners
    [BMS_20S.kicad_pcb, BMS_20S.sch, LM235_1_2.sch]
2020-07-23 updated ufrgs-pill
    [MB1430-G431KBT6-A02_BOM.xlsx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]
2020-08-01 update balancing circuit
    [ACS758.sch, BMS_20S.csv, BMS_24S.kicad_pcb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]
2020-08-01 correctly positioned voltage sensors and balancing
    [BMS_24S.kicad_pcb]
2020-08-01 advances have been made on the voltage sensors
    [BMS_24S.kicad_pcb]
2020-08-03 updated have been made on currents and voltage sensors
    [BMS_24S.kicad_pcb]
2020-08-03 TSAL rounded corners
    [TSAL.kicad_pcb]
2020-08-03 Luz de Freio padrao e-power
    [Luz de Freio.kicad_pcb]
2020-08-04 updates made on BMS
    [BMS_24S.sch, LM235_1_2_3_4.sch, balancing_01.sch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]
2020-08-05 Modified SET/RESET circuit. Added BSPD and AIL circuit.
    [AIL.kicad_pcb, AIL.sch, AIL.step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]
2020-08-07 update all circuits
    [BMS_24S.kicad_pcb, BMS_24S.sch, SET-RESET.csv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]
2020-08-07 add LM235_BRD to git
    [LM235_MOUNT.kicad_pcb, LM235_MOUNT.sch, LM235_MOUNT.step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]
2020-08-07 update tsal
    [TSAL.kicad_pcb]
2020-08-07 review das placas
    [AIL.kicad_pcb, AIL.sch, BSPD.sch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]
2020-08-07 Diferencial Update
    [Diferencial.kicad_pcb, Diferencial.sch]
2020-08-10 schematic update BSPD and new layout not finishet
    [BSPD.kicad_pcb, BSPD.sch]
2020-08-11 AIL schematic and layout att. BSPD layout att.
    [AIL.kicad_pcb, AIL.sch]
2020-08-13 TSAL temp management update
    [TSAL-B_Cu.gbr, TSAL-B_Mask.gbr, TSAL-B_Paste.gbr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]
2020-08-14 Revert "AIL schematic and layout att. BSPD layout att."
    This reverts commit 7e7712d535c298d88471c8cf66961c9a5b232e43.
    [AIL.kicad_pcb, AIL.sch]
2020-08-14 get BSPD
    [BMS_24S.sch, LM235_1_2_3_4.sch, TSAL.kicad_pcb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]
2020-08-14 recover BSPD
    [BSPD.sch]
2020-08-14 update bms pcb
    [BMS_24S-B_Cu.gbr, BMS_24S-B_Mask.gbr, BMS_24S-B_Paste.gbr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]
2020-08-15 update BMS
    [BMS_24S.kicad_pcb, BMS_24S.sch, power.sch]
2020-08-15 Diferencial Layout Update/Main ECU Eeschema
    [BUCK-BOOST KiCad.sch, Diferencial.kicad_pcb, Diferencial.sch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]
2020-08-15 melhorias feitas no BMS
    [BMS_24S.kicad_pcb, BMS_24S.sch, LM235_1_2_3_4.sch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]
2020-08-16 Diferencial Layout Update
    [Diferencial.kicad_pcb, Diferencial.sch]
2020-08-18 Rev. B - BSPD and Rev. B - Set/Reset
    [BSPD.kicad_pcb, BSPD.sch, SET-RESET.kicad_pcb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]
2020-08-23 atualizacao esquematico
    [Luz de Freio.kicad_pcb, Luz de Freio.sch]
2020-08-24 Layout Main ECU and Layout Luz de Freio
    [BUCK-BOOST KiCad.sch, Diferencial.kicad_pcb, Luz de Freio.kicad_pcb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]
2020-08-27 updates made on bms, almost done
    [BMS_24S-B_Cu.gbr, BMS_24S-B_Mask.gbr, BMS_24S-B_Paste.gbr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]
2020-08-29 jlcpcb smt mounting pos file for BMS is update
    [BMS_24S-B_Cu.gbr, BMS_24S-B_Mask.gbr, BMS_24S-B_Paste.gbr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]
2020-08-30 Fixed Schematic and Layout
    [Luz de Freio.kicad_pcb, Luz de Freio.sch, TSAL.sch]
2020-08-30 BSPD att.
    [BSPD.kicad_pcb, BSPD.sch]
2020-08-31 Update Layouyt
    [Luz de Freio.kicad_pcb]
2020-09-01 backup AIL
    [AIL.kicad_pcb, AIL.sch, UFRGS PILL.kicad_pcb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]
2020-09-06 Set/Reset Rev. C
    [BSPD.kicad_pcb, BSPD.sch, SET-RESET.kicad_pcb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]
2020-09-07 Layout Fixes and CAN Connector Added
    [BUCK-BOOST KiCad.sch, Diferencial.kicad_pcb, Diferencial.sch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]
2020-09-07 att set/reset and ail 07/09/2020
    [AIL.kicad_pcb, AIL.sch, SET-RESET.kicad_pcb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]
2020-09-13 Changed Tracks Width
    [Luz de Freio.kicad_pcb]
2020-09-17 Added CAN connectors / Fixes
    [Diferencial.kicad_pcb, Diferencial.sch]
2020-09-18 update pcbs
    [BMS_24S.sch]
2020-09-18 generate gerbers for AIL
    [AIL-B_Cu.gbr, AIL-B_Mask.gbr, AIL-B_Paste.gbr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]
2020-09-18 geretate BSPD gerbers
    [AIL.kicad_pcb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]
2020-09-18 generate diferencial gerbers
    [Diferencial-B_Cu.gbr, Diferencial-B_Mask.gbr, Diferencial-B_Paste.gbr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]
2020-09-18 generate gerbers for brake light
    [LM235_MOUNT-B_Cu.gbr, LM235_MOUNT-B_Mask.gbr, LM235_MOUNT-B_Paste.gbr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]
2020-09-18 generate gerbers and add powertrain pcbs
    [Connectors.sch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]
2020-09-25 powertrain pcbs
    [Gate_Driver_V2-B_Cu.gbr, Gate_Driver_V2-B_Mask.gbr, Gate_Driver_V2-B_SilkS.gbr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]
2020-09-28 dimenssion AIL
    [AIL.kicad_pcb]
2020-10-10 update shutdown
    [AIL.sch, BMS_24S.sch, BSPD.sch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]
2020-11-02 create panel files
    [BMS_24S.csv, baseline.kicad_pcb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]
2020-11-06 add small option panel board
    [Main ECU.kicad_pcb, UFRGS PILL.kicad_pcb, baseline.kicad_pcb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]
2020-12-22 circuito sensor de corrente
    [BSPD.sch, circuito_acs712.kicad_pcb, circuito_acs712.sch]
2021-01-20 placa fdcan
    [FDCAN_MCP2551.kicad_pcb, FDCAN_MCP2551.sch, Luz de Freio.kicad_pcb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]
2021-03-04 esqueatico circuito BMS para monitoramento de temperatura
    [BMS_24S.kicad_pcb, BMS_temperatura.sch, FDCAN_MCP2551.kicad_pcb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]
2021-03-04 att. bms temp
    [BMS_24S.kicad_pcb]
2021-03-08 layout att.1
    [BMS_temperatura.kicad_pcb, LM235_1_2_3_4.sch, power.sch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]
2021-03-11 layout att 2
    [BMS_24S.kicad_pcb]
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2021-03-16 layout bms temp pronto
    [BMS_temperatura.kicad_pcb, BMS_temperatura.sch, LM235_1_2_3_4.sch]
2021-03-19 layout final bms temp
    [BMS_24S.kicad_pcb, BMS_temperatura.kicad_pcb, BMS_temperatura.sch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]
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2021-07-27 Add files via upload
    Divisor de tensão
    [BMS_temperatura.kicad_pcb, BMS_temperatura.sch, LM235_1_2.sch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]
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2021-09-21 BSPD atualizado e charger shutdown adicionado
    [BSPD-B_Cu.gbr, BSPD-B_Mask.gbr, BSPD-B_Paste.gbr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]
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
